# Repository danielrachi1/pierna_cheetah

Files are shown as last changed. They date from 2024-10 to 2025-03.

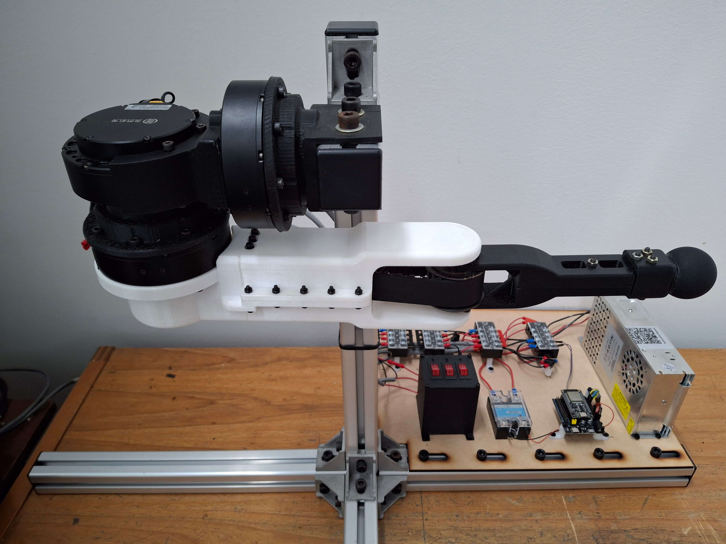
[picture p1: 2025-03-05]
esp32_firmware/spiffs/home_position.jpg

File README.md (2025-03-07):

# Pata de robot cheetah

 Este proyecto se enfoca en el diagnóstico, mantenimiento y mejora de una pierna robótica inspirada en la familia Cheetah, cuyo desarrollo se orienta a su uso en prácticas de laboratorio dentro del programa de Ingeniería Mecatrónica de la Universidad Nacional de Colombia. El estudio abarcó un análisis integral de los componentes mecánicos, eléctricos y de software del sistema. Durante la fase de diagnóstico se identificaron problemas tales como fracturas en componentes estructurales, limitaciones en el control debido al uso de Arduino, cableado desorganizado y la ausencia de un software operativo adecuado. Para solucionar estas incidencias se rediseñaron las piezas mecánicas, se optimizaron las conexiones eléctricas, se sustituyó el Arduino por una ESP32 y se reescribió el firmware utilizando el framework ESP-IDF. Además, se implementaron perfiles de movimiento y mecanismos de seguridad que permiten suavizar las transiciones y evitar golpes violentos. Paralelamente, se desarrollaron guías de laboratorio y se documentó detalladamente el uso, la arquitectura y las pruebas del sistema, facilitando su integración en el entorno educativo.

## Ejemplos de uso

En [este video](https://www.youtube.com/watch?v=v7Muz0Q2M44), se pueden apreciar las funcionalidades principales del robot.

[Este otro video](https://www.youtube.com/watch?v=EpyHmMzFmkk), aunque inicialmente fue grabado para realizar pruebas de funciones de seguridad, también sirve como ejemplo de funcionalidades más avanzadas, como los mecanismos de seguridad.

## Estructura del repositorio

Este reposito se divide en 4 carpetas:

1. **cad**: En esta carpeta se encuentran los modelos de todas las piezas del robot. Se incluyeron tanto archivos .ipt como .stl. Incluir los archivos .ipt hace más fácil modificar las piezas usando inventor, mientras que los .stl son un formato más estandar, para poder visualizarlos en cualquier programa, o hacer más fácil su proceso de impresión.
2. **documentos**: La documentación del proyecto. Estos documentos cubren: El informe del proyecto, documentación del robot y su implementación actual, y las guías de laboratorio diseñadas para el robot. Además de los archivos PDF, se incluye una subcarpeta con todos los ZIPs de los proyectos latex. Esto se hace con el fin de facilitar la edición de cada documento. No se agrega un ZIP del informe.
3. **esp32_firmware**: Esta carpeta contiene el firmware de la ESP32. Es un proyecto creado usando el `ESP-IDF`.
4. **matlab**: Incluye algunos scripts usados para probar la funcionalidad del sistema. Se deja poco documentado a proposito ya que algunos de estos pueden servir como pistas para solucionar los laboratorios planteados.

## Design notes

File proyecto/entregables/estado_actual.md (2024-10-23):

# Análisis del Estado Actual

## Inspección Física y Funcional

### Inspección Visual

- **Estructura**: Los perfiles de aluminio se encuentran estables y en buen estado.
- **Motor 1**: Se mueve con facilidad en un rango aproximado de 180 grados. Sin embargo, el cableado y la estructura limitan su movimiento.
- **Motor 2**: Se desplaza con facilidad en un rango aproximado de 270 grados, con limitación únicamente impuesta por la estructura.
- **Motor 3** (con poleas): Presenta dificultad para moverse, aunque con suficiente fuerza es posible moverlo paso a paso.
- **Soporte del motor 1**: Se encuentra en buen estado.
- **Soporte del motor 2**: Muestra signos de desgaste en la cara orientada hacia el motor 1, posiblemente debido al calor.
- **Soporte del motor 3**: Aunque es una impresión de baja calidad, no presenta fracturas visibles.
- **Cadera**: Se observa una fractura considerable en la pieza impresa.
- **Muslo**: Falta una parte de la impresión. Al parecer, sufrió una fractura previa que fue reparada con pegamento (super bonder).
- **Rodilla**: No se observan daños.
- **Pierna**: Se encuentra en buen estado, aunque uno de los tornillos debería ser más corto.
- **Cableado de los motores**: Parece estar en buenas condiciones, aunque algunos pines se desconectan al realizar ciertos movimientos.
- **Botón de emergencia**: Se percibe una pieza suelta en su interior, pero el botón parece funcionar correctamente.
- **Fuente de alimentación**: En buen estado.
- **Switches**: Están bien conectados y no muestran daños visibles en los cables.
- **Cables de datos de los motores**: Parecen estar en cortocircuito, pero se intuye que esto se debe a que los cables están organizados para ser reconectados a los módulos CAN.

Se tomaron fotografías del estado visual actual. Estas imágenes se encuentran en el repositorio, en la carpeta `proyecto/imagenes/`.

### Funcionalidad Básica

Aunque se propuso hacer un diagnóstico de la funcionalidad actual, esto no fue posible debido al estado en el que se encontraron las conexiones del robot. Para más información sobre la situación de las conexiones, ver el diagnóstico detallado.

## Diagnóstico Detallado

### Integridad de los Circuitos Electrónicos

Durante la inspección del sistema, se encontró que:

- El único cable conectado era el que iba de la fuente de poder a la pared y los cables de la fuente de poder a los motores.
- Los módulos CAN, necesarios para la comunicación entre los distintos componentes del sistema, estaban completamente desconectados y almacenados en una bolsa aparte del resto del sistema.
- La Raspberry Pi estaba guardada en su caja, desconectada del sistema.
- No se encontró el Arduino que controlaba el sistema en el proyecto original. Es probable que este dispositivo perteneciera a uno de los miembros del equipo y haya sido retirado una vez entregado el proyecto.

Durante la inspección del sistema, utilicé un multímetro en modo de continuidad para verificar la conexión entre la fuente de alimentación, los switches y los motores. Se comprobó que todo parecía estar correctamente conectado. Sin embargo, inicialmente el circuito del motor 3 no registraba continuidad, pero esto parecía deberse a una mala conexión en uno de los cables del switch.

Dadas estas circunstancias, intentar encender el sistema o probar cualquier funcionalidad básica hubiera sido prematuro sin antes asegurar que los módulos esenciales estuvieran correctamente conectados y el control del sistema estuviera restablecido.

### Análisis del Software Actual

En el informe del proyecto PAI, se menciona que el código del sistema debería encontrarse en el repositorio de GitHub [https://github.com/jolayam/proyecto_PAI](https://github.com/jolayam/proyecto_PAI). Sin embargo, tras revisar el repositorio, no se encontró el código correspondiente. Al revisar la memoria SD de la Raspberry Pi, se recuperaron algunos archivos, pero noté que faltaban otros importantes. Por ejemplo, el archivo `CAN_COM.cpp` que se menciona en el informe no estaba presente en la información descargada de la tarjeta SD, lo que sugiere que parte del código necesario para la comunicación CAN se ha extraviado. Aunque algunos archivos esenciales están disponibles, es probable que el sistema no funcione correctamente sin este archivo, o al menos requiera una actualización considerable. Dado que la versión del software parece desactualizada, se recomienda realizar una reescritura parcial o total del código, especialmente considerando la posible migración a ROS2 y la implementación de nuevas plataformas, como la ESP32.

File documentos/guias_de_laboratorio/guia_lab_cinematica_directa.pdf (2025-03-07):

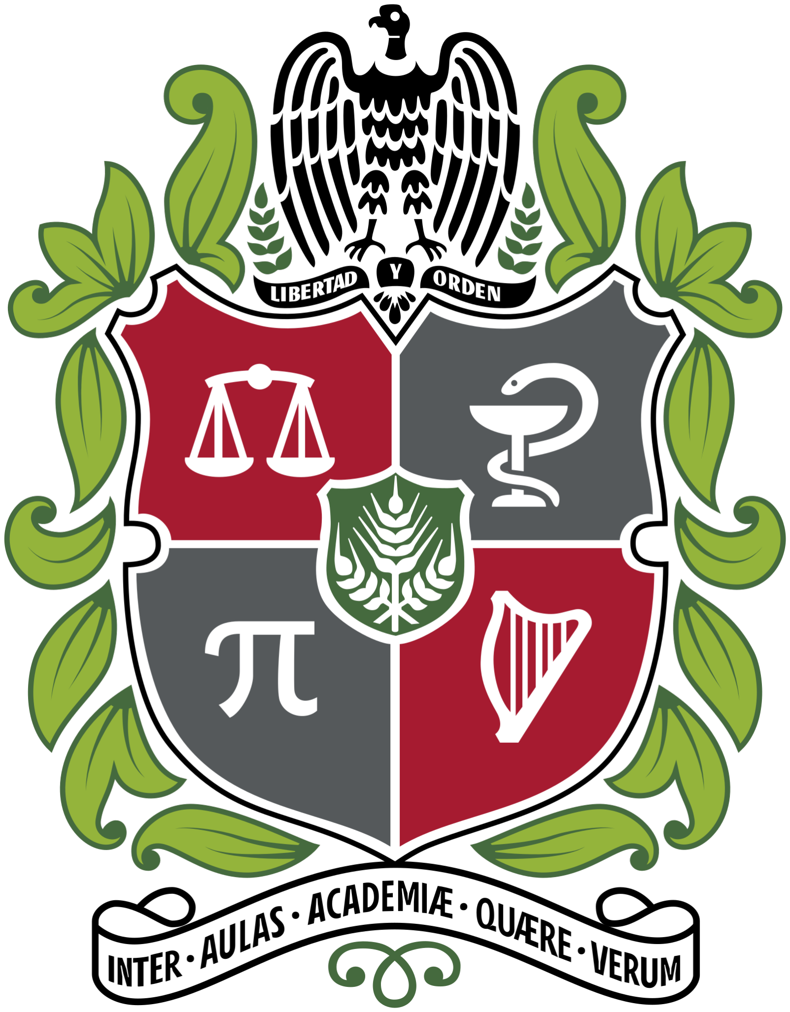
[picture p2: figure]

## Universidad Nacional de Colombia

## Sede Bogotá

### Facultad de Ingeniería

### Departamento de Ingeniería Mecánica y Mecatrónica

# Guía de Laboratorio: Cinemática Directa con la Pata del Robot Cheetah

### 7 de marzo de 2025

## Resultados de Aprendizaje

Formular y modelar la cinemática directa para un robot de tres grados de libertad.

Familiarizarse con la pata del robot cheetah y su funcionamiento.

## Requisitos y Materiales

Documentación del robot.

Conocimientos sobre el sistema DH.

MATLAB.

Pata del robot Cheetah.

Computador con conexión WiFi y al menos un puerto USB-A.

Cable USB-A a USB-C.

## Procedimiento

### 1. Definición y Representación del Robot

Utilice la documentación del robot, disponible en el repositorio: https://github.com/danielrachi1/pierna_cheetah/tree/main/documentos/documentacion, (https://github.com/danielrachi1/pierna_cheetah/tree/main/documentos/documentacion) para obtener la representación DH del robot. Desarrolle el modelo en un archivo MATLAB, utilizando el toolbox de Peter Corke.

### 2. Uso Básico del Robot

¡Aviso de Seguridad! Lea la documentación del robot antes de interactuar con él, para garantizar la seguridad y prevenir daños o lesiones.
Grabe un video en el que se realicen las siguientes acciones:
a) Usando la Interfaz de Usuario
1. Encender el robot.
2. Enviar los siguientes comandos de posición:
a) Motor 1 a 90 grados, con una velocidad de 360 grados por segundo.
b) Motor 2 a -90 grados, con una velocidad de 180 grados por segundo.
c) Motor 3 a -90 grados, con una velocidad de 90 grados por segundo.
3. Apagar el robot.

1

b) Usando la API
1. Encender el robot.
2. Desde el mismo archivo MATLAB, enviar un lote de comandos equivalentes a los de la interfaz.
3. Apagar el robot.

El video debe mostrar el movimiento del robot, la pantalla del computador (ya sea en el navegador o en MATLAB) y los registros (logs) del robot.

## Entregables

Archivo MATLAB con la representación DH y los comandos enviados a la API.

Video demostrativo del uso básico del robot.

2

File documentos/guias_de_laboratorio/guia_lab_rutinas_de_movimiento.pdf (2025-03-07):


## Universidad Nacional de Colombia

## Sede Bogotá

### Facultad de Ingeniería

### Departamento de Ingeniería Mecánica y Mecatrónica

# Guía de Laboratorio: Rutinas de Movimiento con la Pata del Robot Cheetah

### 7 de marzo de 2025

Nota para el profesor: Se recomienda no usar esta guía de laboratorio en el estado actual del robot. La implementación del control a la fecha la hace excelente para procesar comandos individuales por motor, pero no trayectorias completas.

## Resultados de Aprendizaje

Diseñar y programar rutinas de movimiento para la pata del robot.

Validar la ejecución de las rutinas mediante simulación y pruebas en hardware.

## Requisitos y Materiales

Haber realizado el laboratorio de cinemática inversa.

MATLAB.

Pata del robot Cheetah.

Computador conectado a la red local.

Cable USB-A a USB-C.

## Descripción

Se desarrollarán tres rutinas de movimiento para la pata del robot Cheetah: caminar, trotar y correr. Se planificarán las trayectorias, se simularán en MATLAB y se validarán en el Hardware real.

## Procedimiento

### 1. Creación de las rutinas

En un archivo Matlab:

1. Genere trayectorias del robot para cada una de las rutinas. La diferencia entre los tipos de pasos no solo será la velocidad, otros parámetros a tener en cuenta son:

Porcentaje del recorrido tocando el suelo vs en el aire.

Altura máxima alcanzada.

largo del paso.

2. Tome los puntos generados, y aplique las funciones de cinemática inversa para obtener los ángulos necesarios para llegar a cada punto.
3. Construya comandos para enviar al robot y que este ejecute la trayectoria solicitada.

1

### 2. Verificación en hardware

Envíe los comandos generados en el paso anterior al motor. Grabe un video mostrando la ejecución de la rutina.

## Entregables

Archivo MATLAB con la generación de las rutinas de movimiento.

Video demostrativo de la ejecución en hardware.

2

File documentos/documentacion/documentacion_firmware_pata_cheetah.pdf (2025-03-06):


## Universidad Nacional de Colombia

## Sede Bogotá

### Facultad de Ingeniería

### Departamento de Ingeniería Mecánica y Mecatrónica

# Documentación de la Arquitectura del Firmware del Robot Cheetah

## Daniel Esteban Ramirez Chiquillo

### 6 de marzo de 2025

## Índice

1. Introducción | 2
2. Visión General del Sistema | 2
3. Componentes del Sistema | 2
4. Interconexión y Flujo de Datos | 5
5. Consideraciones para Contribuidores | 6
6. Apéndice | 6

## 1. Introducción

Este documento describe la arquitectura interna del firmware desarrollado para la ESP32 que se usa como control del la pata del robot Cheetah. Se abordan los componentes principales del sistema, su funcionalidad, y la forma en que interactúan. La intención es facilitar a futuros contribuyentes la comprensión del código base.

## 2. Visión General del Sistema

El firmware se ejecuta en una plataforma ESP32 y está estructurado en múltiples componentes que se encargan de diferentes tareas, tales como la comunicación en bus CAN, la generación de trayectorias de movimiento, el manejo de comandos de motores, la gestión de la conectividad WiFi y el servicio HTTP, entre otros. A grandes rasgos, el sistema se divide en:

Comunicación y Control de Motores: Involucra la comunicación con los motores a través del bus CAN, el procesamiento de comandos y la generación de trayectorias.

Interfaz de Usuario y Conectividad: Proporciona una API y gestiona la conectividad WiFi y el servicio mDNS.

Coordinación Global: Un controlador de robot de alto nivel que coordina la activación, apagado, y manejo de estados críticos (por ejemplo, modos de recuperación).

## 3. Componentes del Sistema

### 3.1. CAN Bus

Ubicación: ./components/can_bus/ Funcionalidad:

Inicializa el driver TWAI (CAN) de ESP32.

Proporciona funciones para limpiar el bus (can_bus_flush) y enviar mensajes con espera de respuesta (can_bus_request_response).

Define comandos preestablecidos (p.ej., entrar/salir del modo motor, cero del sensor de posición).

Este componente encapsula toda la lógica necesaria para la comunicación CAN, aislando detalles de hardware y facilitando su uso por otros módulos.

### 3.2. Servidor HTTP

Ubicación: ./components/http_server/
Funcionalidad:

Implementa un servidor HTTP basado en la librería esp_http_server.

Sirve contenido estático desde SPIFFS (por ejemplo, index.html, style.css, script.js).

Registra endpoints para comandos del robot (encendido, apagado, recuperación, y comandos de movimiento individuales y por lote).

Este módulo actúa como la puerta de entrada para la interacción remota, permitiendo a los usuarios controlar el robot mediante solicitudes HTTP.

### 3.3. Parser de Mensajes

Ubicación: ./components/message_parser/
Funcionalidad:

Empaqueta datos de comandos en un formato de 8 bytes para la transmisión CAN (pack_cmd).

Desempaqueta respuestas recibidas de los motores (unpack_reply).

Provee funciones de mapeo entre valores flotantes y enteros, adaptando rangos definidos por el hardware.

El parser de mensajes garantiza la correcta codificación y decodificación de los datos intercambiados entre el firmware y los motores.

### 3.4. Perfil de Movimiento

Ubicación: ./components/motion_profile/
Funcionalidad:

Genera trayectorias de movimiento suaves (S-curve) para los motores, basadas en parámetros como velocidad, aceleración y tiempo de muestreo.

Calcula el número de puntos y las posiciones, velocidades y aceleraciones correspondientes para realizar un movimiento controlado.

Este módulo es fundamental para evitar movimientos bruscos, permitiendo una transición gradual en la posición de los motores.

### 3.5. Manejadores de Comandos de Motor

Ubicación: ./components/motor_command_handlers/
Funcionalidad:

Recibe un comando de motor y lo despacha al manejador adecuado (por ejemplo, entrar en modo, salir de modo, cero de sensor, o movimiento).

Valida y procesa parámetros del comando, utilizando internamente el parser de mensajes y el perfil de movimiento.

Este componente centraliza la lógica de decisión para los diferentes tipos de comandos que pueden ejecutarse en cada motor.

### 3.6. Núcleo de Control de Motores

Ubicación: ./components/motor_control_core/
Funcionalidad:

Inicializa y mantiene el estado de cada motor, incluyendo parámetros como la posición actual, estado de compromiso (engaged) y datos de trayectorias activas.

Provee funciones para acceder y modificar el estado de los motores (p.ej., motor_control_get_state y motor_control_move_blocking).

Gestiona comandos en lote, permitiendo la ejecución secuencial y paralela según
corresponda.

Este módulo es el corazón del sistema de control, conectando los comandos de alto nivel con la ejecución física de los motores.

### 3.7. Tarea de Control de Motores

Ubicación: ./components/motor_control_task/ Funcionalidad:

Implementa una tarea de FreeRTOS que se ejecuta continuamente.

Envía puntos de trayectorias a los motores, procesa comandos en lote y monitorea fallos en la comunicación CAN.

Realiza abortos globales en caso de errores críticos, asegurando una operación segura.

Esta tarea opera en segundo plano, orquestando la ejecución de las trayectorias y asegurando la continuidad del control de los motores.

### 3.8. Controlador del Robot

Ubicación: ./components/robot_controller/
Funcionalidad:

Coordina las operaciones globales del robot, como encender y apagar, y la gestión de estados críticos (por ejemplo, el modo de recovery).

Se encarga de iniciar secuencias de activación que involucran la puesta a cero de sensores, el cambio de modos de los motores y la actualización de banderas en NVS.

El controlador del robot actúa como interfaz entre los comandos de usuario y la operación a nivel de motor, asegurando que las acciones críticas se ejecuten en el orden correcto.

### 3.9. Gestor de WiFi

Ubicación: ./components/wifi_manager/
Funcionalidad:

Inicializa la conectividad WiFi en modo estación, configurando la conexión al SSID especificado.

Configura el servicio mDNS para facilitar la detección del dispositivo en la red.

Gestiona eventos de conexión, reconexión y asignación de direcciones IP.

Este componente permite la interacción remota con el robot mediante la red, integrándose con el servidor HTTP.

### 3.10. Programa Principal

Ubicación: ./main/main.c
Funcionalidad:

Es el punto de entrada del firmware, encargado de la inicialización de NVS, montaje de SPIFFS y configuración del hardware (por ejemplo, relés y pines GPIO).

Inicia la conectividad WiFi, el servidor HTTP y lanza la tarea de control de motores.

Verifica el estado previo del sistema (por ejemplo, motores comprometidos de ejecuciones anteriores) para activar el modo de recovery si es necesario.

Este archivo coordina el arranque de todos los componentes, asegurando que el sistema se encuentre en un estado coherente antes de comenzar a operar.

### 3.11. Contenido Estático (SPIFFS)

Ubicación: ./spiffs/
Funcionalidad:

Contiene archivos web (index.html, script.js, style.css) que constituyen la interfaz gráfica para el control remoto del robot.

Estos archivos son servidos por el módulo http_server y permiten al usuario enviar comandos y visualizar notificaciones.

## 4. Interconexión y Flujo de Datos

Los componentes descritos interactúan de la siguiente manera:

1. La interfaz web (contenido en SPIFFS) es servida por el servidor HTTP y permite al usuario enviar solicitudes (por ejemplo, encender/apagar el robot o mover un motor). Esta interfaz realiza solicitudes HTTP al servidor
2. Las solicitudes HTTP son recibidas por el servidor, el cual invoca funciones del controlador del robot. Este controlador valida el estado (por ejemplo, chequeando si se requiere recovery) y dirige la operación.

3. Las operaciones de movimiento se envían al núcleo de control de motores, que actualiza el estado interno de cada motor y, mediante el manejador de comandos de motor, empaqueta y transmite las instrucciones a través del CAN Bus.
4. El parser de mensajes se encarga de convertir los parámetros de los comandos a un formato adecuado para la transmisión y, de forma inversa, interpreta las respuestas de los motores.
5. La tarea de control de motores se ejecuta periódicamente para enviar los puntos de la trayectoria a los motores, gestionar comandos en lote y monitorear la comunicación. En caso de errores, se coordinan abortos globales.
6. El gestor de WiFi y la configuración de mDNS aseguran la conectividad de red, haciendo accesible la interfaz web.
7. Finalmente, el programa principal orquesta la inicialización de todos estos componentes, asegurando que el sistema comience a operar en un estado consistente.

## 5. Consideraciones para Contribuidores

Modularidad: Cada componente está diseñado para ser lo más autónomo posible. Se recomienda mantener esta separación al agregar nuevas funcionalidades.

Comunicación CAN: Cualquier modificación en el formato o en la gestión del bus CAN debe realizarse preferiblemente en el módulo can_bus y ser propagada a través del parser de mensajes.

Generación de Trayectorias: El módulo motion_profile puede extenderse para soportar otros tipos de trayectorias, pero se debe garantizar la compatibilidad con el motor_control_core.

Gestión de Estados: El robot_controller es responsable de los estados críticos (como el modo de recovery). Se debe tener especial cuidado al modificar esta lógica, ya que impacta en la seguridad de la operación.

Interfaz Web: Las modificaciones en la interfaz de usuario deben ser coherentes con los endpoints definidos en el http_server para asegurar una comunicación bidireccional correcta.

## 6. Apéndice

### 6.1. Historial de Revisiones

v1.0 - Documentación inicial de la arquitectura.

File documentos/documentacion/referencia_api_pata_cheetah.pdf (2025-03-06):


## Universidad Nacional de Colombia

## Sede Bogotá

### Facultad de Ingeniería

### Departamento de Ingeniería Mecánica y Mecatrónica

# Referencia de la API de la pata del robot Cheetah

## Daniel Esteban Ramírez Chiquillo

### 6 de marzo de 2025

## Índice

1. Introducción | 2
2. Endpoints de la API | 2
3. Manejo General de Errores | 7
4. Consideraciones de Seguridad | 7
5. Apéndice | 7

## 1. Introducción

Este documento proporciona una referencia completa para la API HTTP implementada en el firmware del robot. La API permite el control remoto del robot a través de un conjunto de endpoints HTTP. Todas las solicitudes y respuestas (excepto el contenido estático) utilizan el formato JSON. Este documento está dirigido a desarrolladores que integren o mantengan el sistema de control del robot.

### 1.1. Visión General

URL Base: El robot es accesible mediante http://cheetah.local)

Versión de la API: 1.0

Formato de Respuesta: JSON (salvo el contenido estático)

Seguridad: Las operaciones críticas verifican el estado de recovery. Si se requiere un procedimiento de recuperación, los comandos se rechazan e indican al usuario las acciones seguras a realizar.

## 2. Endpoints de la API

### 2.1. Endpoints para Contenido Estático

GET / y GET /*

Propósito: Servir archivos estáticos almacenados en el sistema de archivos SPIFFS (por ejemplo, index.html, archivos CSS, JS).
Detalles:

GET / retorna la página principal (index.html).

GET /* actúa como comodín para servir otros archivos. El tipo MIME se establece según la extensión:

- .css → text/css
- .js → application/javascript
- .html → text/html
- Otros archivos se sirven con text/plain.

Manejo de Errores: Si el archivo no se encuentra, se retorna un error 404.

### 2.2. Endpoints de Control de Energía del Robot

POST /api/robot/on

Descripción: Este endpoint enciende el robot. Inicia la secuencia para activar motores, sensores y relés, verificando previamente que el sistema no se encuentre en estado de recovery.
Solicitud:

Método: POST

Cuerpo: Ninguno.

Proceso:

Se verifica que el sistema no esté en estado de recovery.

Se invoca la función interna robot_controller_turn_on().

Respuesta de Éxito:

{
" s t a t u s " : " ok " ,
" message " : " Robot tu rned ON s u c c e s s f u l l y "
}

Respuesta de Error: Si el sistema requiere recovery o ocurre otro fallo: {
" s t a t u s " : " e r r o r " ,
" message " : " Recovery needed . Pl ea s e p h y s i c a l l y power o f f each motor . . . "
}

POST /api/robot/off

Descripción: Apaga el robot, desactivando los motores y relés, siempre que el sistema no se encuentre en estado de recovery.
Solicitud:

Método: POST

Cuerpo: Ninguno.

Proceso:

Se comprueba que el sistema no esté en estado de recovery.

Se invoca la función robot_controller_turn_off().

Respuesta de Éxito:

{
" s t a t u s " : " ok " ,
" message " : " Robot tu rned OFF s u c c e s s f u l l y " }

Respuesta de Error:
{
" s t a t u s " : " e r r o r " ,
" message " : " F ail e d to tu rn o f f " }

### 2.3. Endpoint de Gestión de Recovery

POST /api/recovery/clear

Descripción: Limpia la bandera de recovery del sistema. Este endpoint debe llamarse únicamente después de haber realizado el siguiente procedimiento:

1. Apagar físicamente cada motor (usando el switch o botón de emergencia).
2. Mover manualmente todos los motores a la posición home.
3. Volver a encender los motores.

Solicitud:

Método: POST

Cuerpo: Ninguno.

Respuesta de Éxito (Recovery Limpiado):

{
" s t a t u s " : " ok " ,
" message " : " Recovery c l e a r e d . Motors a r e now c o n si d e r e d s af e . You may now u se o t h e r commands . " }

Respuesta Alternativa (Sin Recovery Necesario):
{
" s t a t u s " : " ok " ,
" message " : "No r e c o v e r y i s needed . System i s normal . " }

Respuesta de Error:
{
" s t a t u s " : " e r r o r " ,
" message " : " F ail e d to c l e a r r e c o v e r y s t a t e " }

### 2.4. Endpoints de Comandos para Motores

POST /api/command/move

Descripción: Envía un comando de movimiento a un motor individual, estableciendo la posición objetivo y la velocidad deseada.
Solicitud:

Método: POST

Cuerpo: Un objeto JSON con la siguiente estructura:
{
" motor_id " : 1 , | // Valo r e s p e rmi ti d o s : 1 , 2 o 3
" p o s i t i o n " : 4 5. 0 , | // P o si ci o n de seada en g rado s
" speed " : 180.0 | // Velocidad en g rado s por segundo
}

Proceso:

Se valida el formato JSON y se comprueba que los valores sean numéricos.

Se verifica que el robot esté encendido y que no se encuentre en estado de recovery.

Se convierten la posición y la velocidad de grados a radianes (multiplicando por π/180).

Se asegura que la velocidad no exceda el límite máximo permitido para el motor (definido en constantes como MOTOR1_MAX_SPEED_DPS, etc.).

Respuesta de Éxito:

{
" s t a t u s " : " ok " ,
" message " : "Move command a c c e p t e d " }

Respuestas de Error:

Si el JSON es inválido o faltan parámetros:
{
" s t a t u s " : " e r r o r " ,
" message " : " Mi s sing o r i n v a l i d ’ p o si ti o n ’ " }

Si la velocidad excede el límite permitido:
{
" s t a t u s " : " e r r o r " ,
" message " : " Speed e x c e e d s maximum allow e d (XXX deg/ s ) " }

Si el robot está apagado:
{
" s t a t u s " : " e r r o r " ,
" message " : " Robot i s o f f . Pl ea s e tu rn on the robo t f i r s t . " }

POST /api/command/batch

Descripción: Permite enviar un lote de comandos de movimiento para uno o más motores. Los comandos dirigidos a motores diferentes se ejecutan en paralelo, mientras que los comandos para un mismo motor se procesan de forma secuencial.
Solicitud:

Método: POST

Cuerpo: Un objeto JSON que contenga un arreglo batch con cada comando:

{
" batch " : [
{ " motor_id " : 1 , " p o s i t i o n " : 45 , | " speed " : 100 } ,
{ " motor_id " : 2 , " p o s i t i o n " : 90 , | " speed " : 50 } ,
{ " motor_id " : 3 , " p o s i t i o n " : 135 , " speed " : 25} ,
{ " motor_id " : 1 , " p o s i t i o n " : 0 , | " speed " : 50 } ,
{ " motor_id " : 2 , " p o s i t i o n " : 0 , | " speed " : 75 } ,
{ " motor_id " : 3 , " p o s i t i o n " : 0 , | " speed " : 100}
]
}

Proceso:

1. Se verifica que no exista otro lote en ejecución.
2. Se validan individualmente todos los comandos (tipos numéricos, rangos válidos y motor_id correcto).
3. Se convierten las posiciones y velocidades de grados a radianes.
4. Se asignan y encolan los comandos para cada motor.
5. Se espera a que todos los comandos se ejecuten o se produzca un error.

Respuesta de Éxito: Se retorna un resumen para cada motor:

{
" gl o b al _ s t a t u s " : " ok " ,
" motors " : [
{
" motor_id " : 1 ,
" s t a t u s " : " ok " ,
" commands_executed " : 2
} ,
{
" motor_id " : 2 ,
" s t a t u s " : " ok " ,
" commands_executed " : 2
} ,
{
" motor_id " : 3 ,
" s t a t u s " : " ok " ,
" commands_executed " : 2
}
]
}

Respuestas de Error:

Si algún comando del lote tiene un formato incorrecto:

{
" gl o b al _ s t a t u s " : " e r r o r " ,
" message " : " I n v a l i d command fo rma t i n batch " }

Si ya existe un lote en ejecución:
{
" gl o b al _ s t a t u s " : " e r r o r " ,
" message " : " Batch al r e a d y i n p r o g r e s s "
}

Si un motor específico encuentra un error durante la ejecución, su resumen incluirá: {
" motor_id " : X,
" s t a t u s " : " e r r o r " ,
" e r ro r_me s sage " : " D e t ail e d e r r o r d e s c r i p t i o n " , " commands_executed " : Y
}

## 3. Manejo General de Errores

Todas las respuestas de la API incluyen un campo status con los valores «ok» o «error»

Las respuestas de error incluyen un campo message con una explicación legible para el usuario.

Se utilizan códigos de estado HTTP estándar (por ejemplo, 200 para éxito, 404 para no encontrado, 500 para errores internos).

## 4. Consideraciones de Seguridad

Verificación del Estado de Recovery: Antes de ejecutar comandos que modifiquen el comportamiento de los motores, la API verifica si el sistema se encuentra en estado de recovery. En tal caso, se rechaza la operación y se notifica al cliente.

Validación de Entradas: Todos los endpoints que aceptan payloads JSON realizan una validación rigurosa de los datos para prevenir operaciones inseguras (por ejemplo, movimientos que excedan los límites físicos).

Procesamiento Secuencial en Batch: Para las operaciones en lote, los comandos dirigidos al mismo motor se procesan de forma secuencial.

## 5. Apéndice

### 5.1. Historial de Revisiones

v1.0 - Versión inicial de la referencia de la API.

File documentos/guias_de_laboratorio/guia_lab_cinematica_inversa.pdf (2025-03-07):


## Universidad Nacional de Colombia

## Sede Bogotá

### Facultad de Ingeniería

### Departamento de Ingeniería Mecánica y Mecatrónica

# Guía de Laboratorio: Cinemática Inversa con la Pata del Robot Cheetah

### 7 de marzo de 2025

## Resultados de Aprendizaje

Formular y modelar el problema de cinemática inversa para un robot de tres grados de libertad.

Implementar algoritmos de cinemática inversa en MATLAB.

Validar algoritmos de cinemática inversa en un entorno real.

## Requisitos y Materiales

Haber realizado el laboratorio de cinemática directa.

Conocimientos de cinemática en robótica.

MATLAB.

Pata del robot Cheetah.

Computador con conexión WiFi y al menos un puerto USB-A.

Cable USB-A a USB-C.

## Descripción

Esta práctica se centra en derivar e implementar la cinemática inversa para la pata del robot Cheetah, validando los resultados en el hardware real.

## Procedimiento

### 1. Cinemática Inversa (Analítica)

Derive las ecuaciones que relacionen la posición deseada del efector (x, y, z) con los ángulos de las articulaciones (θ1, θ2, θ3). Puede emplear métodos analíticos o geométricos, justificando el procedimiento.

### 2. Verificación en Software

Escriba un archivo MATLAB con:

Las ecuaciones derivadas y su respectiva justificación.
La validación del modelo: calcule los ángulos para una posición dada y verifique, mediante la cinemática directa, que la posición obtenida se aproxima a la posición objetivo.

Realice la cinemática inversa del robot con el toolbox de Peter Corke. ¿Nota diferencias en los ángulos obtenidos? ¿Los ángulos obtenidos son posibles de aplicar en el espacio de trabajo del robot?

1

### 3. Verificación en Hardware

Seleccione tres puntos (x, y, z) dentro del espacio de trabajo. Utilice el mismo archivo MATLAB para obtener los ángulos, construir el comando y ejecutar el movimiento mediante la API. Grabe un video siguiendo el mismo estilo del laboratorio anterior.

## Entregables

Archivo MATLAB con la implementación de la cinemática inversa.

Video demostrativo de la ejecución en el robot.

2

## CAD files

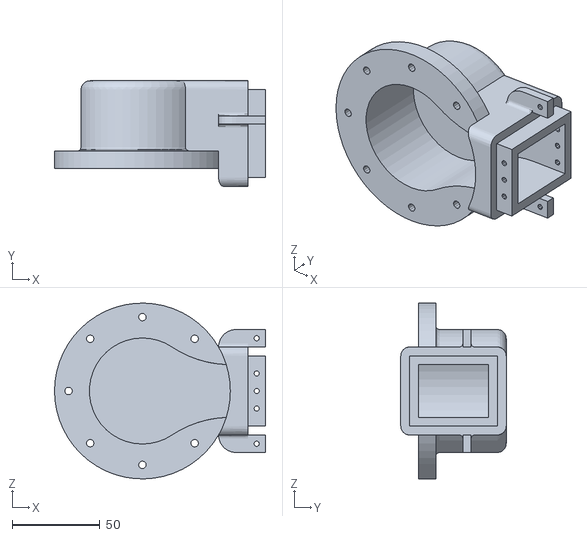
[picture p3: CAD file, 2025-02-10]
cad/stl/cadera.stl
120.0 x 60.0 x 100.0

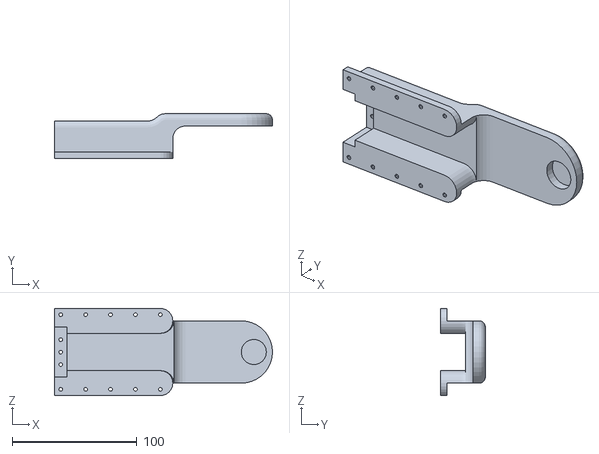
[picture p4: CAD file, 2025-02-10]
cad/stl/muslo.stl
175.0 x 36.0 x 70.0

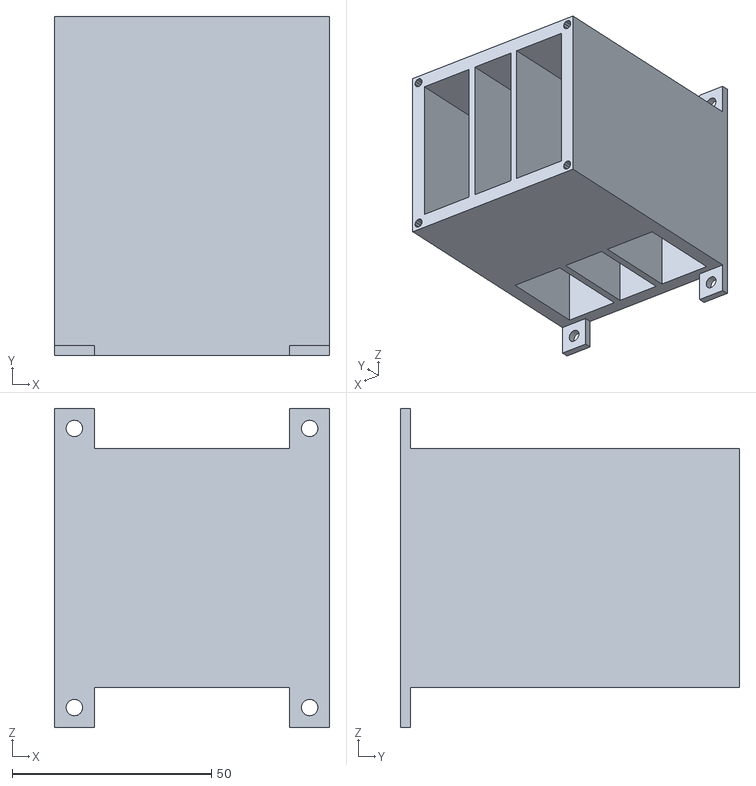
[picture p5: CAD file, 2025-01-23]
cad/stl/switch_case_box.stl
69.0 x 85.0 x 80.0

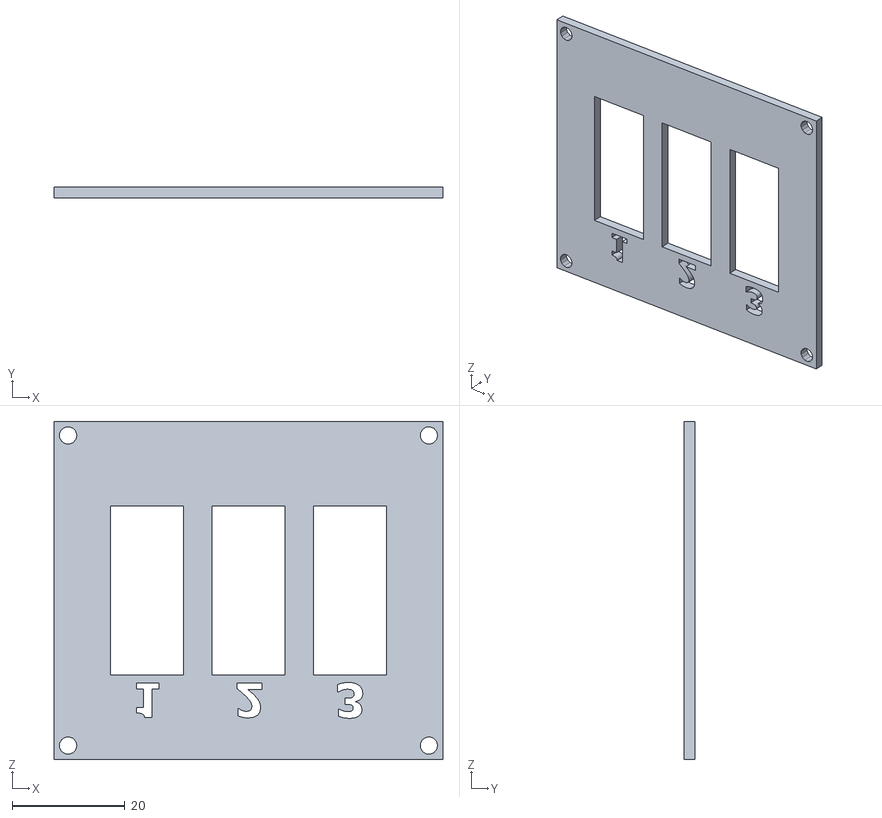
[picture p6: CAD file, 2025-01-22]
cad/stl/switch_case_lid.stl
69.0 x 2.00 x 60.0

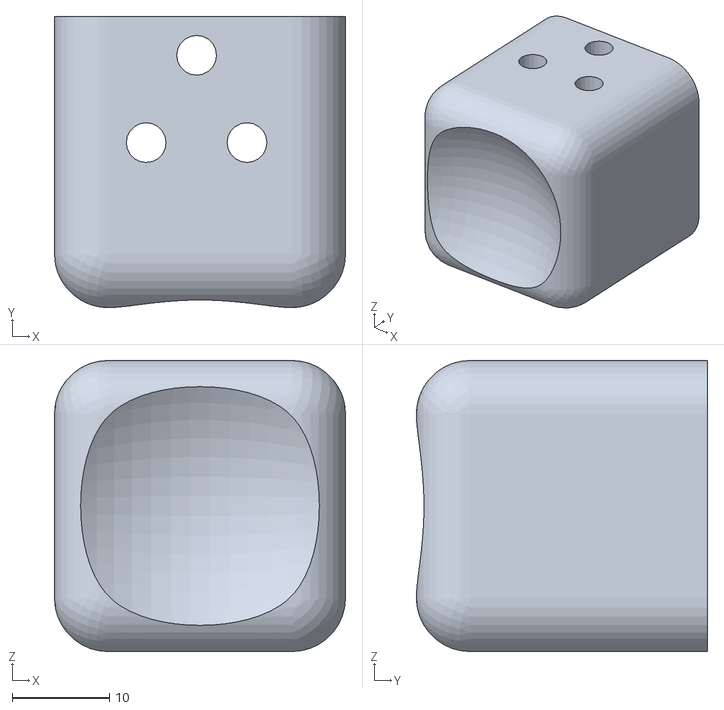
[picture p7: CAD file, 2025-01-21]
cad/stl/pie.stl
30.0 x 30.0 x 30.0

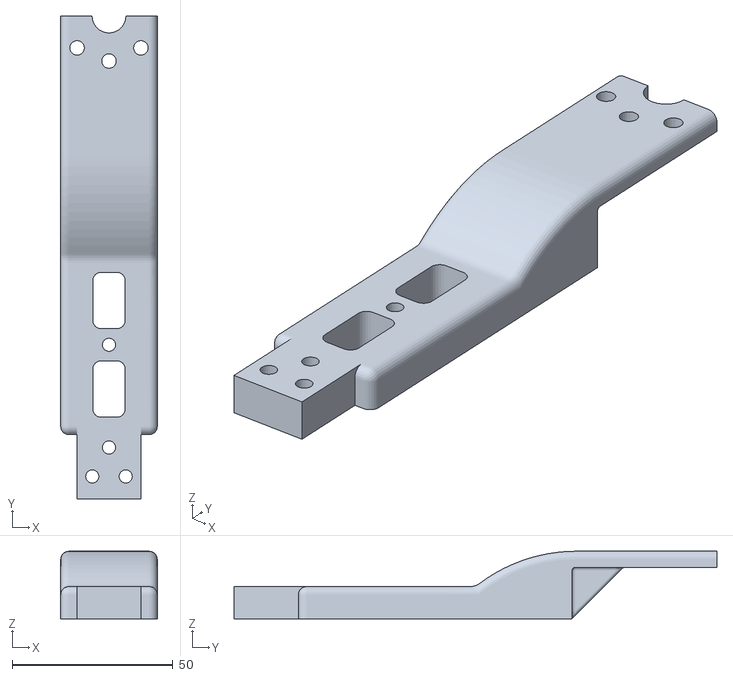
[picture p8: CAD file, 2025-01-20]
cad/stl/pierna_baja.stl
30.0 x 150.0 x 21.0

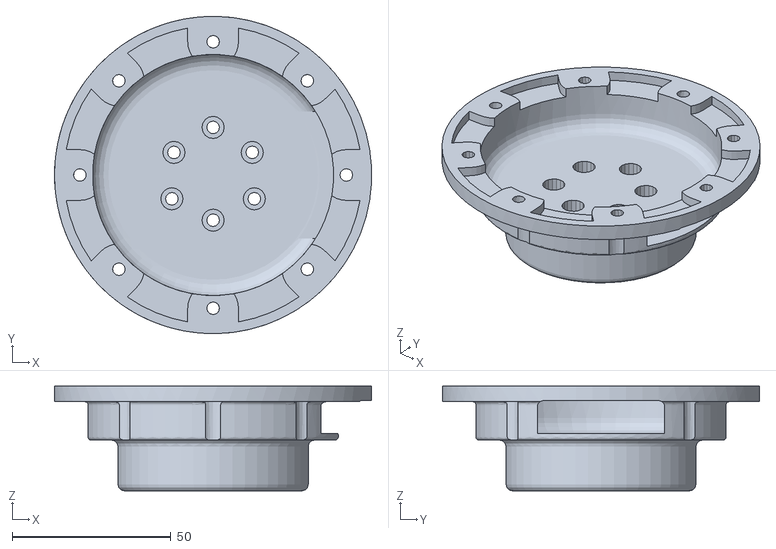
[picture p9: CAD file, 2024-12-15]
cad/stl/acople_motor2.stl
99.9 x 100.0 x 33.0

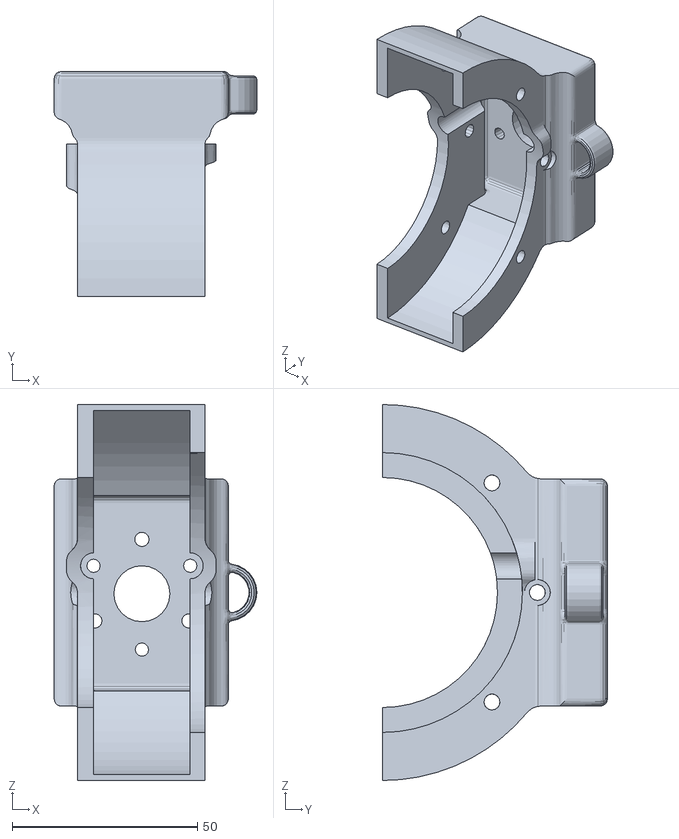
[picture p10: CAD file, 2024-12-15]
cad/stl/acople_motor3.stl
54.7 x 60.7 x 101.4

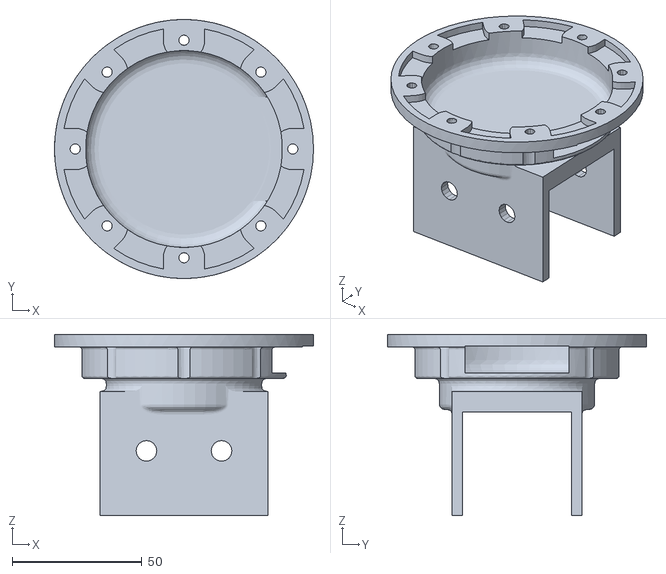
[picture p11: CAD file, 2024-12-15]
cad/stl/acople_motor1.stl
100.0 x 100.0 x 70.0

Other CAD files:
cad/ipt/acople_motor1.ipt
cad/ipt/acople_motor2.ipt
cad/ipt/acople_motor3.ipt
cad/ipt/board_layout.ipt
cad/ipt/cadera.ipt
cad/ipt/muslo.ipt
cad/ipt/pie.ipt
cad/ipt/pierna_baja.ipt
cad/ipt/switch_case_box.ipt
cad/ipt/switch_case_lid.ipt

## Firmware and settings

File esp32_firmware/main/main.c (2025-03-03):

#include "freertos/FreeRTOS.h"
#include "freertos/task.h"
#include "esp_system.h"
#include "esp_log.h"
#include "nvs_flash.h"
#include "esp_spiffs.h"
#include "wifi_manager.h"
#include "can_bus.h"
#include "http_server.h"
#include "motor_control_core.h"
#include "motor_control_task.h"
#include "driver/gpio.h"
#include "robot_controller.h"

#define LOG_TAG "ESP32_FIRMWARE"
#define TASK_STACK_SIZE 4096

void app_main(void)
{
    // Initialize NVS
    esp_err_t ret = nvs_flash_init();
    if (ret == ESP_ERR_NVS_NO_FREE_PAGES || ret == ESP_ERR_NVS_NEW_VERSION_FOUND)
    {
        ESP_ERROR_CHECK(nvs_flash_erase());
        ret = nvs_flash_init();
    }
    ESP_ERROR_CHECK(ret);

    // Mount SPIFFS for file serving
    esp_vfs_spiffs_conf_t spiffs_conf = {
        .base_path = "/spiffs",
        .partition_label = NULL,
        .max_files = 5,
        .format_if_mount_failed = true};
    ret = esp_vfs_spiffs_register(&spiffs_conf);
    if (ret != ESP_OK)
    {
        ESP_LOGE(LOG_TAG, "Failed to mount SPIFFS (%s)", esp_err_to_name(ret));
        return;
    }
    ESP_LOGI(LOG_TAG, "SPIFFS mounted successfully");

    // Initialize robot controller
    robot_controller_init();

    // Initialize CAN bus
    ESP_ERROR_CHECK(can_bus_init());

    // Initialize motor control
    motor_control_init();
    xTaskCreate(motor_control_task, "motor_control_task", TASK_STACK_SIZE, NULL, 10, NULL);

    // If leftover motors were engaged, force shutdown now
    if (robot_controller_get_motors_engaged_flag())
    {
        ESP_LOGW(LOG_TAG, "Detected leftover engaged motors. Entering recovery mode.");
        robot_controller_set_recovery_needed(true);
    }

    // Start Wi-Fi and mDNS
    ESP_ERROR_CHECK(wifi_manager_start());
    ESP_ERROR_CHECK(wifi_manager_setup_mdns());

    // Start HTTP server
    http_server_start();

    // Configure relay GPIO as OUTPUT but ensure it's off initially
    gpio_reset_pin(GPIO_NUM_4);
    gpio_set_direction(GPIO_NUM_4, GPIO_MODE_OUTPUT);
    gpio_set_level(GPIO_NUM_4, 0);

    ESP_LOGI(LOG_TAG, "Main setup complete.");
}

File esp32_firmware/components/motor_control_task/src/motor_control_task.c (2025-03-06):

#include "motor_control_task.h"
#include "motor_control_core.h"
#include "motor_command_handlers.h"
#include "robot_controller.h"
#include "can_bus.h"
#include "message_parser.h"
#include "motion_profile.h"

#include "freertos/FreeRTOS.h"
#include "freertos/task.h"
#include "esp_log.h"
#include <string.h>
#include <math.h>

static const char *TAG = "MOTOR_CONTROL_TASK";

// We keep a separate failure counter for each motor:
static int s_motor_failure_count[NUM_MOTORS] = {0};

/**
 * @brief If we detect a batch error or repeated CAN failures, abort all batch commands system-wide.
 */
static void global_batch_abort(void)
{
    ESP_LOGE(TAG, "Global batch abort triggered due to error.");
    for (int i = 0; i < NUM_MOTORS; i++)
    {
        motor_state_t *st = motor_control_get_state(i + 1);
        if (st->batch_commands)
        {
            free(st->batch_commands);
            st->batch_commands = NULL;
        }
        st->batch_count = 0;
        st->batch_index = 0;
        st->batch_error = true;
    }
    motor_control_set_batch_in_progress(false);
    ESP_LOGI(TAG, "All batch commands aborted.");
}

/**
 * @brief Send the next point of the trajectory (if active) and parse the feedback.
 *        Increments the motor's trajectory index. If done, frees the old trajectory.
 */
static void process_motor_trajectory(motor_state_t *state)
{
    // If this motor does not have an active trajectory, nothing to do.
    if (!state->trajectory_active)
    {
        return;
    }

    // If the trajectory is active but we've already consumed all points,
    // then we’re done.
    if (state->trajectory_index >= state->trajectory_points)
    {
        return;
    }

    // Grab the next trajectory setpoint
    motion_profile_point_t *pt = &state->trajectory[state->trajectory_index];

    // Retrieve motor gains
    float kp = 0.0f;
    float kd = 0.0f;
    switch (state->motor_id)
    {
    case 1:
        kp = KP1;
        kd = KD1;
        break;
    case 2:
        kp = KP2;
        kd = KD2;
        break;
    case 3:
        kp = KP3;
        kd = KD3;
        break;
    default:
        break; // Should never happen
    }

    // Convert user-space angles to hardware angles
    float hw_pos = from_user_angle(state->motor_id, pt->position);
    float hw_vel = from_user_angle(state->motor_id, pt->velocity);

    // Build the CAN message
    uint8_t can_msg_data[8];
    memset(can_msg_data, 0, sizeof(can_msg_data));
    pack_cmd(hw_pos, hw_vel, kp, kd, 0.0f, can_msg_data);

    // Transmit & wait for the motor’s response
    twai_message_t response;
    esp_err_t err = can_bus_request_response(can_msg_data, 8, state->motor_id, &response);
    if (err != ESP_OK)
    {
        // Record the failure
        int idx = state->motor_id - 1;
        s_motor_failure_count[idx]++;
        ESP_LOGE(TAG, "Motor %d: CAN TX/RX failed. Consecutive errors=%d",
                 state->motor_id, s_motor_failure_count[idx]);
        // After too many failures, force a global shutdown + batch abort
        if (s_motor_failure_count[idx] >= 3)
        {
            robot_controller_handle_motor_error(state->motor_id);
            global_batch_abort();
        }
        return;
    }

    // On success, reset this motor’s failure counter
    s_motor_failure_count[state->motor_id - 1] = 0;

    // If we got a 6-byte reply, parse the feedback to update state->current_position
    if (response.data_length_code == 6)
    {
        motor_reply_t reply = {0};
        unpack_reply(response.data, &reply);

        float user_angle = to_user_angle(state->motor_id, reply.position);
        state->current_position = user_angle;

        ESP_LOGI(TAG,
                 "Motor %d: Traj idx=%d/%d => hw=(%.4f pos, %.4f vel) => user=(%.4f), feedbackCur=%.2f",
                 state->motor_id, state->trajectory_index + 1, state->trajectory_points,
                 reply.position, reply.velocity, user_angle, reply.current);
    }

    // Advance to the next point in the trajectory
    state->trajectory_index++;
    if (state->trajectory_index >= state->trajectory_points)
    {
        // We have reached the final point
        state->trajectory_active = false;
        if (state->trajectory)
        {
            motion_profile_free_trajectory(state->trajectory);
            state->trajectory = NULL;
        }
        ESP_LOGI(TAG, "Motor %d: Trajectory finished.", state->motor_id);

        // If we’re currently processing a batch MOVE command, *now* it's fully done
        if (state->batch_commands)
        {
            state->batch_index++;
            if (state->batch_index >= state->batch_count)
            {
                free(state->batch_commands);
                state->batch_commands = NULL;
                state->batch_count = 0;
                state->batch_index = 0;
                ESP_LOGI(TAG, "Motor %d: Finished all batch commands.", state->motor_id);
            }
        }
    }
}
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

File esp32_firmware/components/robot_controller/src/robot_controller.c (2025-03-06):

#include "robot_controller.h"

#include <stdio.h>
#include <string.h>
#include "esp_log.h"
#include "esp_err.h"
#include "nvs.h"
#include "nvs_flash.h"

#include "can_bus.h"
#include "motor_control_core.h"     
#include "motor_command_handlers.h" 
#include "driver/gpio.h"            

static const char *TAG = "ROBOT_CONTROLLER";

#define NVS_NAMESPACE "storage"
#define NVS_KEY_MOTORS_ENGAGED "motors_engaged"

/*
 * Internal state:
 *   s_robot_engaged: false means robot is OFF; true means robot is ON/engaged.
 *   s_recovery_needed: true if a previous run left motors engaged (improper shutdown),
 *                      meaning the user must physically power off motors, home them,
 *                      then call /api/recovery/clear.
 */
static bool s_robot_engaged = false;
static bool s_recovery_needed = false;

bool robot_controller_is_engaged(void)
{
    return s_robot_engaged;
}

bool robot_controller_is_recovery_needed(void)
{
    return s_recovery_needed;
}

void robot_controller_set_recovery_needed(bool needed)
{
    s_recovery_needed = needed;
}

static esp_err_t set_motors_engaged_flag(bool engaged)
{
    nvs_handle_t handle;
    esp_err_t err = nvs_open(NVS_NAMESPACE, NVS_READWRITE, &handle);
    if (err != ESP_OK)
    {
        ESP_LOGE(TAG, "Failed to open NVS: %s", esp_err_to_name(err));
        return err;
    }
    err = nvs_set_u8(handle, NVS_KEY_MOTORS_ENGAGED, (uint8_t)(engaged ? 1 : 0));
    if (err == ESP_OK)
    {
        err = nvs_commit(handle);
    }
    nvs_close(handle);
    return err;
}

esp_err_t robot_controller_clear_recovery(void)
{
    // When the user calls this endpoint, we assume they have physically:
    // 1. Powered off the motors (via switches/emergency stop)
    // 2. Manually moved the motors to the home position
    // 3. Then turned them on again.
    s_recovery_needed = false;
    // Also clear the NVS flag to reflect that motors are no longer engaged.
    set_motors_engaged_flag(false);
    ESP_LOGI(TAG, "Recovery cleared. The user indicates motors are physically safe.");
    return ESP_OK;
}

bool robot_controller_get_motors_engaged_flag(void)
{
    nvs_handle_t handle;
    esp_err_t err = nvs_open(NVS_NAMESPACE, NVS_READONLY, &handle);
    if (err != ESP_OK)
    {
        ESP_LOGE(TAG, "Failed to open NVS for reading: %s", esp_err_to_name(err));
        return false;
    }
    uint8_t val = 0;
    err = nvs_get_u8(handle, NVS_KEY_MOTORS_ENGAGED, &val);
    nvs_close(handle);
    if (err == ESP_OK)
    {
        return (val == 1);
    }
    return false;
}

// Relay control helper
static esp_err_t relay_set(bool enable)
{
    ESP_LOGI(TAG, "Relay %s", enable ? "ON" : "OFF");
    gpio_set_level(GPIO_NUM_4, enable ? 1 : 0);
    return ESP_OK;
}

void robot_controller_init(void)
{
    // On a fresh boot, default to off and no recovery needed.
    s_robot_engaged = false;
    s_recovery_needed = false;
}

esp_err_t robot_controller_turn_on(void)
{
    ESP_LOGI(TAG, "Turn On requested...");

    // Do not allow turning on if recovery is needed.
    if (s_recovery_needed)
    {
        ESP_LOGE(TAG,
                 "Cannot turn on while 'recovery needed' is set. "
                 "User must physically power off each motor, manually home them, then call /api/recovery/clear.");
        return ESP_ERR_INVALID_STATE;
    }

    if (s_robot_engaged)
    {
        ESP_LOGW(TAG, "Robot is already engaged, ignoring");
        return ESP_ERR_INVALID_STATE;
    }

    // 1) Relay ON
    relay_set(true);

    // 2) Zero sensors on all motors
    for (int i = 1; i <= NUM_MOTORS; i++)
    {
        twai_message_t response;
        esp_err_t err = can_bus_send_zero_pos_sensor(i, &response);
        if (err != ESP_OK)
        {
            ESP_LOGE(TAG, "Zero sensor failed on motor %d: %s", i, esp_err_to_name(err));
            robot_controller_turn_off();
            return ESP_FAIL;
        }
    }

    // 3) Enter motor mode on all motors
    for (int i = 1; i <= NUM_MOTORS; i++)
    {
        motor_command_t cmd = {
            .motor_id = i,
            .cmd_type = MOTOR_CMD_ENTER_MODE,
            .position = 0.0f // Not used for enter mode
        };
        esp_err_t err = motor_control_handle_command(&cmd);
        if (err != ESP_OK)
        {
            ESP_LOGE(TAG, "Enter mode failed on motor %d: %s", i, esp_err_to_name(err));
            robot_controller_turn_off();
            return ESP_FAIL;
        }
    }

    // 4) Set NVS flag
    esp_err_t err = set_motors_engaged_flag(true);
    if (err != ESP_OK)
    {
        ESP_LOGE(TAG, "Failed to set NVS motors_engaged: %s", esp_err_to_name(err));
        robot_controller_turn_off();
        return ESP_FAIL;
    }

    // 5) Mark robot as engaged (won't lock if we don't set this flag before the for loop)
    s_robot_engaged = true;

    // 6) "Lock" motors on zero position
    for (int i = 3; i >= 1; i--)
    {
        esp_err_t err = motor_control_move_blocking(i, 0.0f, pdMS_TO_TICKS(1000));
        if (err != ESP_OK)
        {
            ESP_LOGW(TAG, "Motor %d failed to reach home (or timed out). Err: %s", i, esp_err_to_name(err));
            robot_controller_turn_off();
            return ESP_FAIL;
        }
    }

    ESP_LOGI(TAG, "Robot successfully turned on. Engaged = true");
    return ESP_OK;
}

esp_err_t robot_controller_turn_off(void)
{
    ESP_LOGI(TAG, "Turn Off requested...");

    // Even if s_robot_engaged is false, we continue with cleanup.
    if (s_robot_engaged)
    {
        // 1) Move all motors to home (0.0). Done in reverse (3 to 1) because the other way is more
        // likely to cause collisions.
        for (int i = 3; i >= 1; i--)
        {
            esp_err_t err = motor_control_move_blocking(i, 0.0f, pdMS_TO_TICKS(5000));
            if (err != ESP_OK)
            {
                ESP_LOGW(TAG, "Motor %d failed to reach home (or timed out). Err: %s", i, esp_err_to_name(err));
            }
        }

        // 2) Exit motor mode on all motors
        for (int i = 1; i <= NUM_MOTORS; i++)
        {
            twai_message_t response;
            esp_err_t err = can_bus_send_exit_mode(i, &response);
            if (err != ESP_OK)
            {
                ESP_LOGW(TAG, "Exit mode failed on motor %d: %s", i, esp_err_to_name(err));
            }
        }
    }
    else
    {
        ESP_LOGW(TAG, "Robot is physically off, skipping move and exit steps.");
    }

    // 3) Disable relay
    relay_set(false);

    // 4) Clear the engaged flag in NVS
    esp_err_t err_nvs = set_motors_engaged_flag(false);
    if (err_nvs != ESP_OK)
    {
        ESP_LOGW(TAG, "Failed to clear NVS flag. err: %s", esp_err_to_name(err_nvs));
    }

    // 5) Mark robot as off
    s_robot_engaged = false;
    ESP_LOGI(TAG, "Robot is now OFF.");
    return ESP_OK;
}
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

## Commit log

2024-09-17 Agregar formato de definicion de trabajo de grado
2024-09-17 Agregar imagenes de la inspeccion visual
2024-09-24 Organizar carpeta de proyecto
2024-10-07 Crear archivo de notas
    Creé un archivo en donde llevaré apuntes generales del proyecto. Una
    especie de bitácora. También tomé algunos apuntes relacionados al
    informe del proyecto de PAI de la pata.
    Llevo este registro para tener presente alguna información que me puede
    ser relevante más adelante, pero que no es suficientemente formal como
    para incluir en algún entregable.
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2024-11-26 Agregar hoja de cálculo para conversion de floats e ints
    [unit_to_float_and_float_to_int.ods]
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2024-11-26 Escribir funcionalidad básica en main
    El programa ahora puede:
    1. Leer comandos desde UART.
    2. Convertir estos comandos en paquetes CAN.
    3. Auto enviarse el paquete CAN.
    4. Leer el paquete CAN.
    Se agregaron logs a lo largo de todo el proceso para poder analizarlo
    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
2024-11-27 Fix: change torque to current in reply_message_t
    [message_parser.h]
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2024-11-27 Fix: unpack_reply function
    [unit_to_float_and_float_to_int.ods]
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2024-11-28 Escribir firmware básico
    Se escribió firmware que utiliza la ESP32 como servidor. Se pueden
    enviar datos al servidor conectandose a la misma red wifi y abriendo
    su IP en un navegador.
    Al enviar los comandos desde el navegador, la ESP32 maneja la recepción
    del comando, el parsing del JSON, la construcción del mensaje CAN, y
    envía el mensaje CAN al motor.
    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
2024-12-01 Agregar archivos viejos faltantes
    Estos archivos estaban en la microSD de la RPi. Pero había olvidado
    agregarlos al repo.
2024-12-02 Separar HTML, CSS y JS del archivo main
    [partitions.csv]
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2024-12-03 Arreglar valores máximos y minimos de pos, vel, etc
    [message_parser.h]
2024-12-10 Agregar perfil de movimiento
    No estoy seguro de si ya funciona, pero compila, los tests pasan y los
    logs se ven bien.
2024-12-10 Mejorar logs de trayectoria, mejorar UI
    La mejora de la UI incluye una nueva seccion en donde solo se envía la
    pos deseada. Se re-incorporó enviar comandos "raw" al motor.
2024-12-10 fix: Selección de ID en move to position
    [main.c]
2024-12-15 Importar carpeta del proyecto PAI232G2E
    [Acople motor perpendicular v1.ipt, Acople motor perpendicular v1.stl, Acople motor perpendicular v1.stp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]
2024-12-16 Agregar modelos 3D listos para imprimir
    [orca_slicer_project.3mf]
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2025-01-20 CAD (STL) del eslabón 3
    [eslabon3.stl.stl]
2025-01-20 Agregar archivo ipt del eslabon 3
    [eslabon3.ipt, eslabon3.stl]
2025-01-20 Agregar archivos CAD de la zapato-herramienta
    [tool_shoe.ipt, tool_shoe.stl]
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2025-01-20 tool_shoe v2
    [tool_shoe.ipt, tool_shoe.stl]
2025-01-21 Archivos CAD del case para la ESP32 y el mod CAN
    [esp_can_case.ipt, esp_can_case.stl, esp_can_case_lid.ipt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]
2025-01-21 tool_shoe v3
    [tool_shoe.ipt, tool_shoe.stl]
2025-01-21 Iteracion de ESP+CAN case
    [esp_can_case.ipt, esp_can_case.stl, esp_can_case_lid.ipt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]
2025-01-22 Agregar CADs de la tapa del panel para los switches
    [panel_switches.ipt, panel_switches.stl]
2025-01-23 Agregar archivos CAD de la caja para los switches
    [switch_pannel_box.ipt, switch_pannel_box.stl]
2025-01-23 Agregar archivos CAD del board_layout (corte MDF)
    [board_layout.dwg, board_layout.ipt]
2025-01-28 Arreglar sugerencias del linter de Markdown
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2025-01-29 Mejorar seguridad agrando Exit Motor Mode on boot
2025-01-31 Agregar CAD de pulley_case
    [pulley_case.ipt, pulley_case.stl]
2025-02-03 Agregar CAD pulley case part 1
    El archivo que no es por partes (pulley case) es muy grande para mi impresora.
    [pulley_case_part_1.ipt, pulley_case_part_1.stl]
2025-02-03 Arreglo pulley_case_part_1
    [pulley_case_part_1.ipt, pulley_case_part_1.stl]
2025-02-04 Agregar CAD de las ultimas 2 partes del pulley case
    [pulley_case.iam, pulley_case_part_2.ipt, pulley_case_part_2.stl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]
2025-02-04 Agregar hoja de cálculo para estimar largo polea
    [pulley_to_bearing_center_distance.ods]
2025-02-05 Mejorar la seguridad del sistema
    Implementé flags que me permiten tener registro de cuándo cada motor
    está activo. Ahora los motores se desactivan cada vez que la ESP32
    bootea.
    Sin estas medidas de seguridad, se corre el riesgo de que la pata de
    movimientos abruptos. Si mi implementación es correcta, ahora todos los
    movimientos que haga la pata deben usar los perfiles de movimiento.
    [main.c]
2025-02-05 Arreglar pulley_case_part3
    [pulley_case.iam, pulley_case_part_3.ipt, pulley_case_part_3.stl]
2025-02-06 Arreglar pulley case
    [pulley_case.iam, pulley_case_part_1.ipt, pulley_case_part_1.stl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]
2025-02-06 ajustar pulley case para impresora
    [pulley_case.iam, pulley_case_part_1.ipt, pulley_case_part_1.stl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]
2025-02-07 Mejorar pulley case
    Se redujo la longitud, se incremento el diametro del espacio de la polea, se amplio la tolerancia del conector de ambas partes
    [pulley_case.iam, pulley_case_part_1.ipt, pulley_case_part_1.stl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]
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2025-02-09 Asegurar cambio correcto de la flag de engagement
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2025-02-10 Corregir medidas pulley_case
    [pulley_case.iam, pulley_case_part_1.ipt, pulley_case_part_1.stl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]
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2025-02-12 Actualizar el motor state cuando se indica zero pos
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2025-02-22 Limpiar y organizar el repositorio
    [Acople motor perpendicular v1.ipt, Acople motor perpendicular v1.stl, Acople motor perpendicular v1.stp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]
2025-02-22 Organizar y renombrar archivos CAD
    [acople_motor1.ipt, acople_motor1.stl, acople_motor2.ipt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]
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2025-02-26 Agregar parametro de velocidad
    Será útil al generar las rutinas de movimiento, para diferenciar
    caminar, trotar y correr.
2025-02-26 Arreglos de encendido y apagado
    [main.c, robot_controller.c]
2025-02-26 Arreglos de comandos de posicion por web
    [http_server.c]
2025-02-27 Eliminar estados de robot: initializing, error, shutting down
    [robot_controller.c]
2025-02-27 Eliminar estado de robot: operating
    Cada motor se ocupa, no todo el robot.
2025-02-27 Agregar logica de recovery y bloqueo
    Para cuando se reinicie la ESP32 sin apagar los motores.
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2025-02-28 Arreglar logica de recovery
    [main.c]
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2025-03-02 Agregar archivo con ejemplos de llamados a la api
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2025-03-02 Cambiar input de velocidad a grados por segundo
2025-03-02 Arreglar tamaño de labels para enviar comandos
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2025-03-03 Subir el archivo correcto del muslo
    [muslo.ipt]
2025-03-04 Arreglar errores de compilación
    [http_server.c]
2025-03-04 Eliminar timeout en batch
    ahora solo envía el JSON si acaba todos los comandos o alguno manda un
    error.
    [http_server.c]
2025-03-04 Arreglo de batches
2025-03-05 Agregar scripts de matlab, solucion simplificada de los labs
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2025-03-06 Agregar documentacion del robot y referencia de la api
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
